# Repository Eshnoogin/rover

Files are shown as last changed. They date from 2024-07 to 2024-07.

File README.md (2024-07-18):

# Version 1



This version of the rover has to be plugged in to work, or be powered by a battery that supplies more than 5 volts. It integrates three motor drivers and a gyroscope to correct for the motors' speeds being slightly off from each other.  It has three almost 3d printed omniwheels, which only need ball bearings and screws. It uses an ESP-32 dev board to drive the motors. It also has ESP-NOW integration, which is needed in order to be driven by an external joystick.

# Version 2 - WIP
roverv2
This version of the rover supports being completely battery powered with two AA batteries. It is powered by an ESP32-S3, which uses a 3.3 volt regulator. The regulator is also powering the gyroscope and camera *eventually*. Onboard the PCB, there is also a 5v regulator to move the motors. Unlike V1 of the rover, these wheels are completely 3d printed. Unfortunatly, as of right now, the USB connection stopped working after a short and the motors are stuck spinning until shutdown.

# Board 

Version 2 of the board has four layers, with the two internal planes being ground planes, unlike version 1, which just has two layers and a ground fill on each. It uses a Texas Instraments DRV8832DGQR and TPS61040DBVRG4 to drive the motors and boost voltage, respectively. The gyroscope being used is part of the MPU-6050 and, of course, the main component of V2 is the ESP32-S3-WROOM module.

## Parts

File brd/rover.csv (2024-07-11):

Id | Designator | Footprint | Quantity | Designation | Supplier and ref
1 | R11,R12 | res1206 | 2 | 200kOhms
2 | R3,R1,R2 | res1206 | 3 | 2.87kOhms
3 | D1,D2 | D_SOD-123 | 2 | Schtokky
4 | C7 | cap1206 | 1 | 22uF
5 | R7,R19,R8,R9 | res1206 | 4 | 10kOhms
6 | P1 | PinHeader_1x02_P2.54mm_Vertical | 1 | ~
7 | P3,P4,P2 | twopad | 3 | ~
8 | C11,C13,C5,C10 | cap1206 | 4 | 4.7uF
9 | R6,R5,R4 | res1206 | 3 | 400mOhms
10 | C6 | cap1206 | 1 | 3.3pF
11 | C2,C1,C3 | cap1206 | 3 | 10uF
12 | J1 | MOLEX_1050170001 | 1 | 1050170001
13 | U2,U3,U1 | IC_XTR111AIDGQRG4 | 3 | DRV8832DGQR
14 | R10 | res1206 | 1 | 620kOhms
15 | U7 | XCVR_ESP32S3WROOM1N8R8 | 1 | ESP32-S3-WROOM-1-N4
16 | R13 | res1206 | 1 | 330kOhms
17 | U4,U5 | PinSocket_1x08_P2.54mm_Vertical | 2 | ~
18 | S2,S1 | SW_SKQGAFE010 | 2 | SKQGAFE010
19 | L1 | IND_SRR1240-100M | 1 | 3.3uH
20 | C4,C9 | cap1206 | 2 | .1uF
21 | C8 | cap1206 | 1 | 1uF
22 | U9,U6 | SOT95P280X145-5N | 2 | TPS61040DBVRG4
23 | L2 | IND_SRR1240-100M | 1 | 10uH

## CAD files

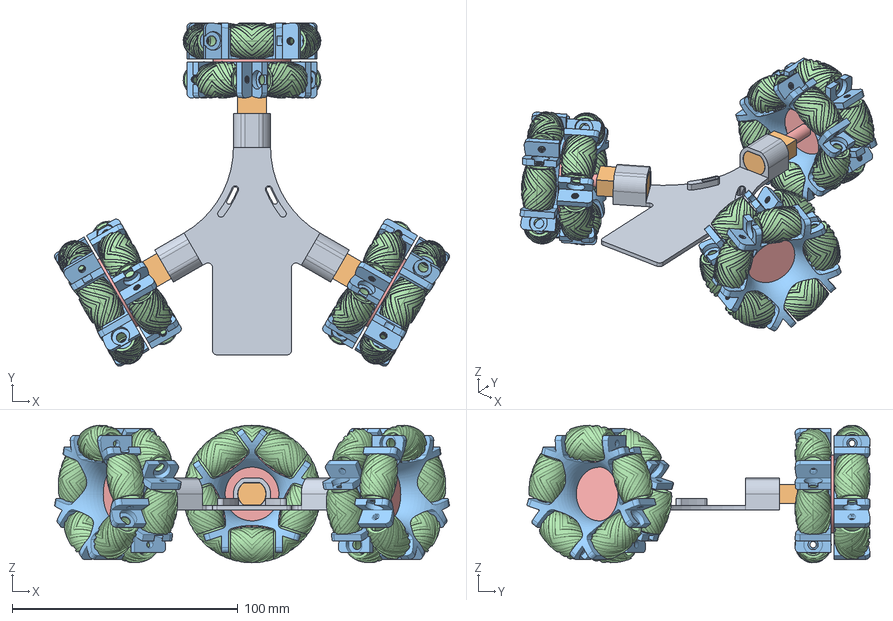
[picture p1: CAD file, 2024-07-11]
cad/rover.step
175.1 x 152.2 x 61.0 mm
motor x 3
base x 6
wheel x 30
middleJoint x 3

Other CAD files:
cad/rover.f3z

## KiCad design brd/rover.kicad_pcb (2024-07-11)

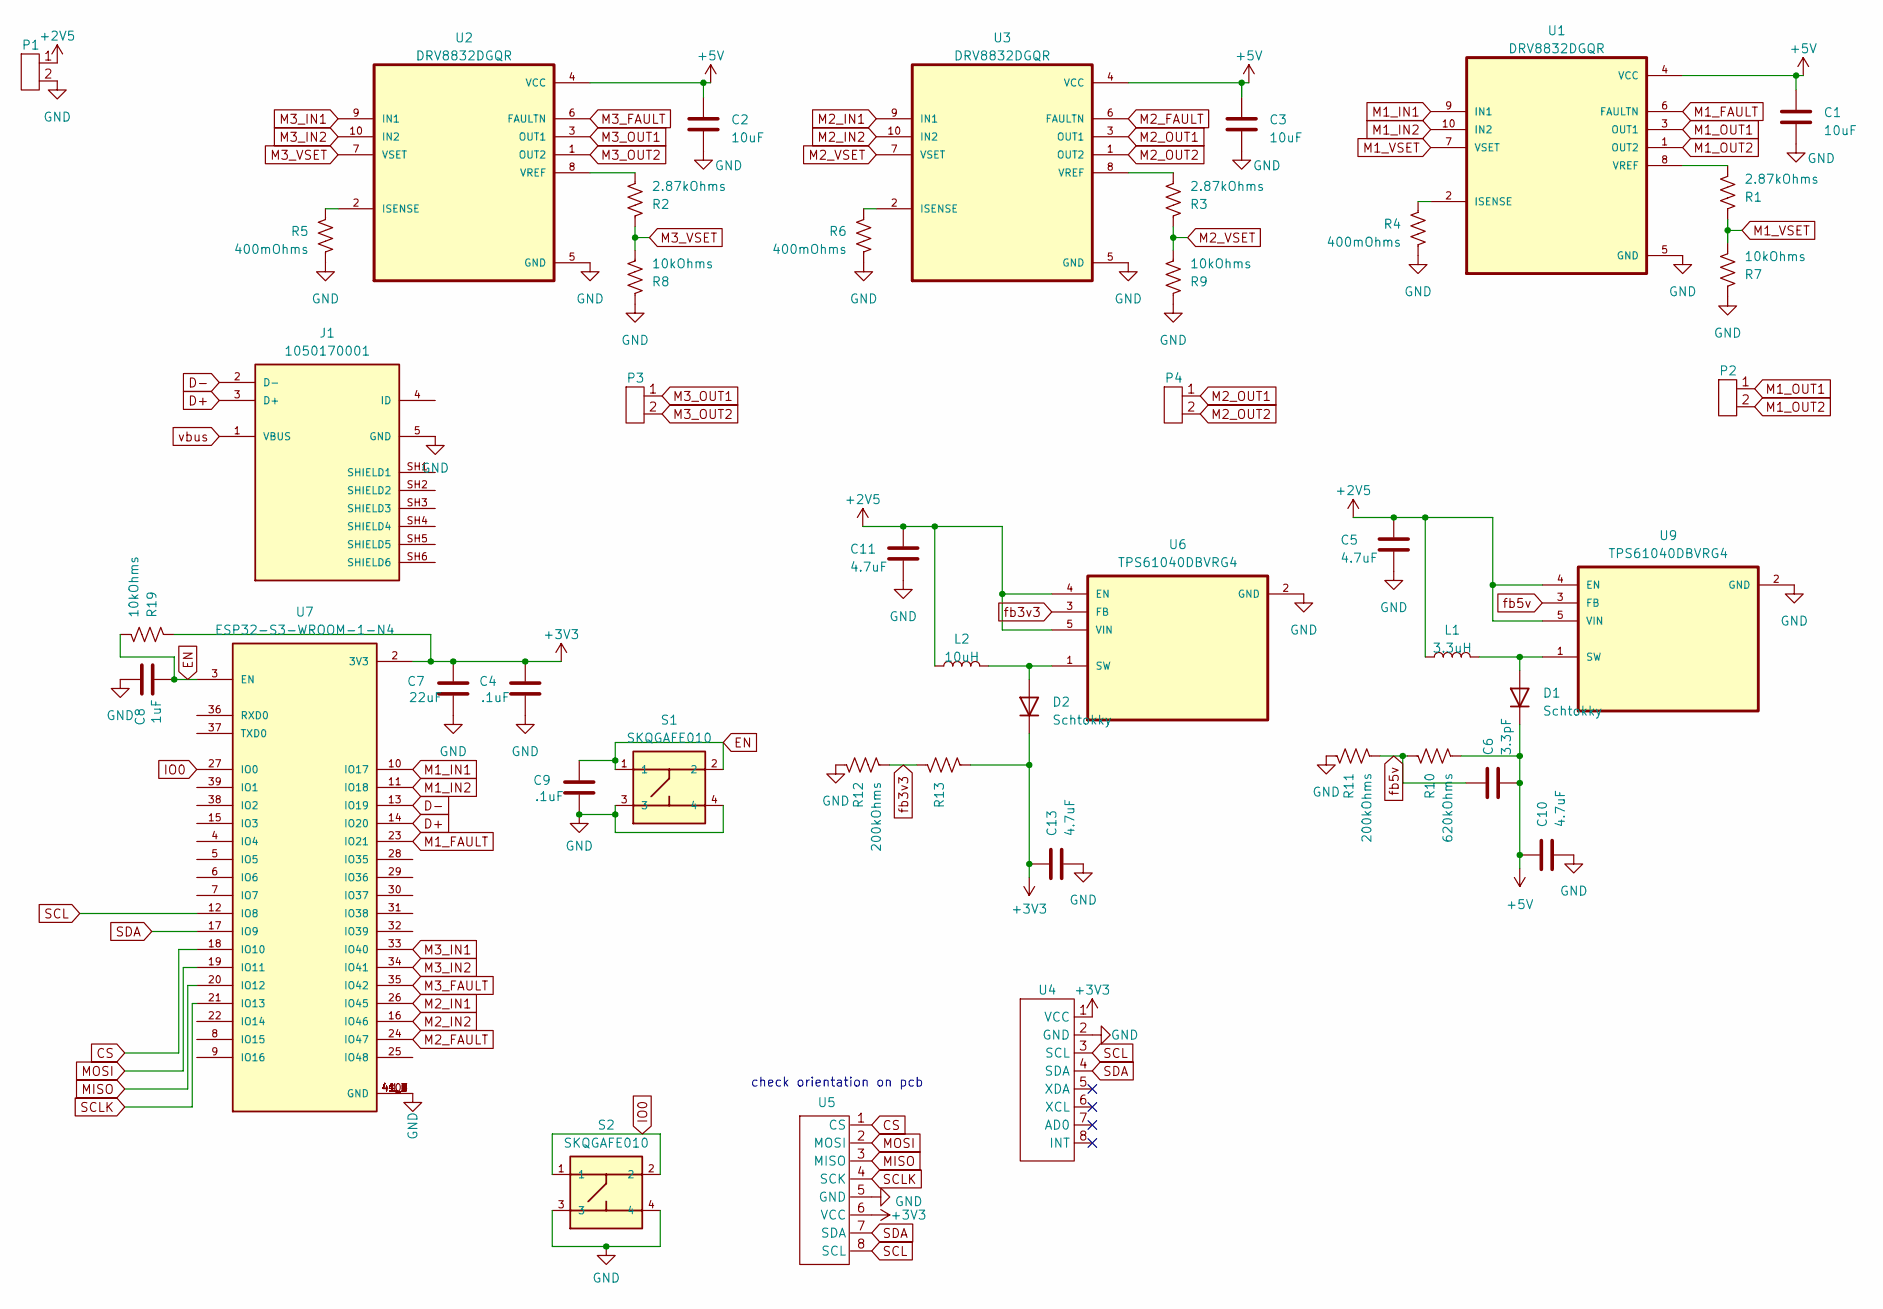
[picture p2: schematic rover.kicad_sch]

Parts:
C1, C2, C3: 10uF; cap1206
C4, C9: .1uF; cap1206
C5, C10, C11, C13: 4.7uF; cap1206
C6: 3.3pF; cap1206
C7: 22uF; cap1206
C8: 1uF; cap1206
D1, D2: Schtokky; D_SOD-123
J1: 1050170001; MOLEX_1050170001; PARTREV F
L1: 3.3uH; IND_SRR1240-100M
L2: 10uH; IND_SRR1240-100M
P1: PinHeader_1x02_P2.54mm_Vertical
P2, P3, P4: twopad
R1, R2, R3: 2.87kOhms; res1206
R4, R5, R6: 400mOhms; res1206
R7, R8, R9, R19: 10kOhms; res1206
R10: 620kOhms; res1206
R11, R12: 200kOhms; res1206
R13: 330kOhms; res1206
S1, S2: SKQGAFE010; SW_SKQGAFE010; PART_REV B1
U1, U2, U3: DRV8832DGQR; IC_XTR111AIDGQRG4
U4, U5: PinSocket_1x08_P2.54mm_Vertical
U6, U9: TPS61040DBVRG4; SOT95P280X145-5N
U7: ESP32-S3-WROOM-1-N4; XCVR_ESP32S3WROOM1N8R8; PARTREV v1.0

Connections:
+2V5: C5.1, C11.1, L1.1, L2.1, P1.1, U6.4 (EN), U6.5 (VIN), U9.4 (EN), U9.5 (VIN)
+3V3: C4.1, C7.1, C13.1, D2.1 (K), R13.2, R19.1, U4.1 (VCC), U5.6 (VCC), U7.2 (3V3)
+5V: C1.1, C2.1, C3.1, C6.2, C10.1, D1.1 (K), R10.2, U1.4 (VCC), U2.4 (VCC), U3.4 (VCC)
CS: U5.1 (CS), U7.18 (IO10)
D+: J1.3 (D+), U7.14 (IO20)
D-: J1.2 (D-), U7.13 (IO19)
EN: C8.2, C9.1, R19.2, S1.1, S1.2, U7.3 (EN)
GND: C1.2, C2.2, C3.2, C4.2, C5.2, C7.2, C8.1, C9.2, C10.2, C11.2, C13.2, J1.5 (GND), P1.2, R4.2, R5.2, R6.2, R7.1, R8.1, R9.1, R11.1, R12.1, S1.3, S1.4, S2.3, S2.4, U1.5 (GND), U2.5 (GND), U3.5 (GND), U4.2 (GND), U5.5 (GND), U6.2 (GND), U7.1 (GND), U7.40 (GND), U7.41_1 (GND), U7.41_2 (GND), U7.41_3 (GND), U7.41_4 (GND), U7.41_5 (GND), U7.41_6 (GND), U7.41_7 (GND), U7.41_8 (GND), U7.41_9 (GND), U9.2 (GND)
IO0: S2.1, S2.2, U7.27 (IO0)
M1_FAULT: U1.6 (FAULTN), U7.23 (IO21)
M1_IN1: U1.9 (IN1), U7.10 (IO17)
M1_IN2: U1.10 (IN2), U7.11 (IO18)
M1_OUT1: P2.1, U1.3 (OUT1)
M1_OUT2: P2.2, U1.1 (OUT2)
M1_VSET: R1.1, R7.2, U1.7 (VSET)
M2_FAULT: U3.6 (FAULTN), U7.24 (IO47)
M2_IN1: U3.9 (IN1), U7.26 (IO45)
M2_IN2: U3.10 (IN2), U7.16 (IO46)
M2_OUT1: P4.1, U3.3 (OUT1)
M2_OUT2: P4.2, U3.1 (OUT2)
M2_VSET: R3.1, R9.2, U3.7 (VSET)
M3_FAULT: U2.6 (FAULTN), U7.35 (IO42)
M3_IN1: U2.9 (IN1), U7.33 (IO40)
M3_IN2: U2.10 (IN2), U7.34 (IO41)
M3_OUT1: P3.1, U2.3 (OUT1)
M3_OUT2: P3.2, U2.1 (OUT2)
M3_VSET: R2.1, R8.2, U2.7 (VSET)
MISO: U5.3 (MISO), U7.20 (IO12)
MOSI: U5.2 (MOSI), U7.19 (IO11)
unnamed: D1.2 (A), L1.2, U9.1 (SW)
unnamed: D2.2 (A), L2.2, U6.1 (SW)
unnamed: R4.1, U1.2 (ISENSE)
unnamed: R1.2, U1.8 (VREF)
unnamed: R5.1, U2.2 (ISENSE)
unnamed: R2.2, U2.8 (VREF)
unnamed: R6.1, U3.2 (ISENSE)
unnamed: R3.2, U3.8 (VREF)
SCL: U4.3 (SCL), U5.8 (SCL), U7.12 (IO8)
SCLK: U5.4 (SCK), U7.21 (IO13)
SDA: U4.4 (SDA), U5.7 (SDA), U7.17 (IO9)
fb3v3: R12.2, R13.1, U6.3 (FB)
fb5v: C6.1, R10.1, R11.2, U9.3 (FB)
vbus: J1.1 (VBUS)

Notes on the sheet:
check orientation on pcb

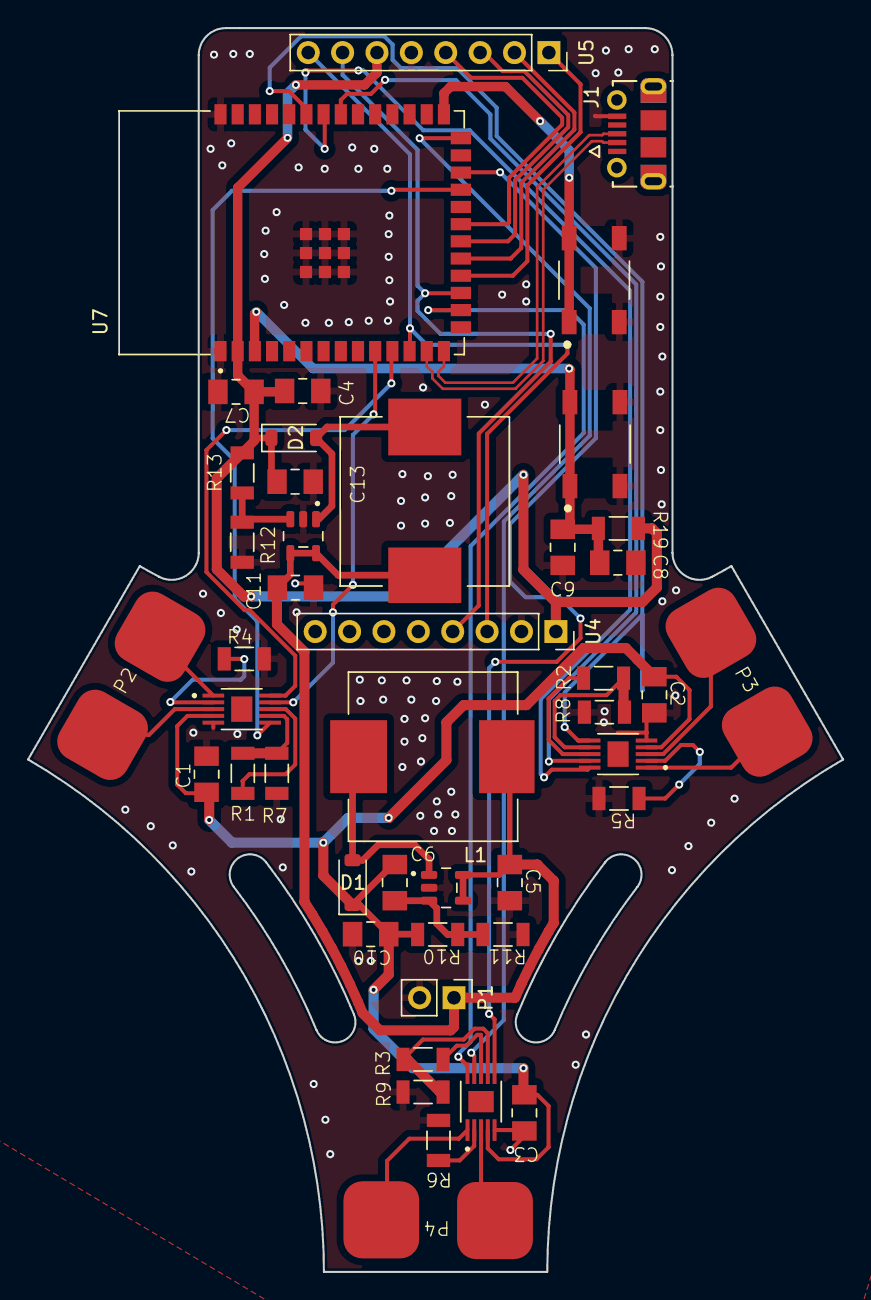
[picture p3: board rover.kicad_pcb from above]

Board: 4 copper layers, 60.2 x 91.9 mm, 45 parts (0 on the bottom side), 42 nets.

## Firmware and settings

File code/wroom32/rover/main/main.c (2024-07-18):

#include <stdio.h>
#include <math.h>

#include "freertos/FreeRTOS.h"
#include "esp_log.h"
#include "driver/i2c_master.h"
#include "driver/mcpwm_timer.h"
#include "driver/mcpwm_oper.h"
#include "driver/mcpwm_gen.h"
#include "driver/mcpwm_cmpr.h"
#include "esp_timer.h"
#include "driver/spi_master.h"

#include "driver/gpio.h"

#include "imu.h"
#include "common.h"
#include "motor.h"
#include "comm.h"
#include "cam.h"

#define TAG "RVR"

#define M1_IN1 26
#define M1_IN2 27
#define M2_IN1 16
#define M2_IN2 17
#define M3_IN1 32
#define M3_IN2 25

i2c_master_bus_handle_t i2c_mst_bus_handle;

imu_handle_t imu;

motor_handle_t motor1;
motor_handle_t motor2;
motor_handle_t motor3;

float measured_z_rotation;
SemaphoreHandle_t z_rot_mutex;

void handle_imu()
{
    while (1)
    {
        imu_update_gyro(&imu);

        CRITICAL_SECTION(imu.imu_mutex, 15, {
            CRITICAL_SECTION(z_rot_mutex, 15, {
                if (fabs(imu.gyro_z) > 10){ // some noise will be present in the raw sensor data
                    measured_z_rotation += imu.gyro_z;
                }
            });
        });

        vTaskDelay(10 / portTICK_PERIOD_MS);
    }
}

void handle_movement()
{
    while (1)
    {
        float v1 = 0;
        float v2 = 0;
        float v3 = 0;

        // read gyroscope data
        CRITICAL_SECTION(imu.imu_mutex, 15, {
            bool do_move = true;
            CRITICAL_SECTION(z_rot_mutex, 15, {
                if(fabs(measured_z_rotation) < 300){
                    do_move = false;
                }
                if(do_move){
                    if(fabs(measured_z_rotation) < 450){ //helps the robot face the center in less steps
                        v1 += (measured_z_rotation < 0) ? -0.25 : 0.25;
                        v2 += (measured_z_rotation < 0) ? -0.25 : 0.25;
                        v3 += (measured_z_rotation < 0) ? -0.25 : 0.25;     
                    }else{  
                        v1 += (measured_z_rotation < 0) ? -0.5 : 0.5;
                        v2 += (measured_z_rotation < 0) ? -0.5 : 0.5;
                        v3 += (measured_z_rotation < 0) ? -0.5 : 0.5;        
                    }
                }
            });
        });

        // read espnow data
        CRITICAL_SECTION(last_command.cmd_mutex, 15, {
            if(last_command.time + 20000 > esp_timer_get_time()){
                v1 += cos(last_command.direction);
                v2 += -.5 * cos(last_command.direction) + ((sqrt(3) / 2) * sin(last_command.direction));
                v3 += -.5 * cos(last_command.direction) - ((sqrt(3) / 2) * sin(last_command.direction));

                // normalize values
                float v_max = fmax(fabs(v1), fmax(fabs(v2), fabs(v3)));
                if (v_max != 0)
                {
                    v1 /= v_max;
                    v2 /= v_max;
                    v3 /= v_max;
                }
            }
        });

        ESP_LOGI(TAG, "M1: %f M2: %f M3: %f", v1, v2, v3);

        // move motors
        motor_move_at(&motor1, v1);
        motor_move_at(&motor2, v2);
        motor_move_at(&motor3, v3);

        vTaskDelay(pdMS_TO_TICKS(25));
    }
}

void app_main(void)
{
    // setup i2c for gyroscope and camera
    i2c_master_bus_config_t i2c_mst_config = {
        .clk_source = I2C_CLK_SRC_DEFAULT,
        .i2c_port = -1,
        .scl_io_num = 22,
        .sda_io_num = 21,
        .glitch_ignore_cnt = 7,
    };
    ESP_ERROR_CHECK(i2c_new_master_bus(&i2c_mst_config, &i2c_mst_bus_handle));

    // init imu
    z_rot_mutex = xSemaphoreCreateMutex();
    TaskHandle_t handle_imu_handler;
    imu_init(&imu);
    xTaskCreate(handle_imu, "handle_imu", 4096, NULL, 1, &handle_imu_handler);

    // configure timer, shared across all pwms
    ledc_fade_func_install(0);
    ledc_timer_config_t ledc_timer = {
        .speed_mode = LEDC_LOW_SPEED_MODE,
        .timer_num = LEDC_TIMER_0,
        .duty_resolution = LEDC_TIMER_8_BIT,
        .freq_hz = 25,
        .clk_cfg = LEDC_AUTO_CLK};
    ledc_timer_config(&ledc_timer);

    // init motors
    motor_init(&motor1, M1_IN1, M1_IN2, LEDC_CHANNEL_0, LEDC_CHANNEL_1, &ledc_timer);
    motor_init(&motor2, M2_IN1, M2_IN2, LEDC_CHANNEL_2, LEDC_CHANNEL_3, &ledc_timer);
    motor_init(&motor3, M3_IN1, M3_IN2, LEDC_CHANNEL_4, LEDC_CHANNEL_5, &ledc_timer);

    // setup esp-now
    espnow_init();

    // init movement
    TaskHandle_t handle_movement_handler;
    xTaskCreate(handle_movement, "handle_movement", 2048, NULL, 1, &handle_movement_handler);

    ESP_LOGI(TAG, "startSTART");
    for(int i=0; i<=255; i++){
        ESP_LOGI(TAG, "probing 0x%.2x", i);
        if(i2c_master_probe(i2c_mst_bus_handle, i, 100) == ESP_OK){
            ESP_LOGW(TAG, "DEV FOUND AT 0x%.2x", i);
        }
    }

    //init SPI bus
    spi_bus_config_t spi_bus_config = {
        .data0_io_num=-1,
        .data1_io_num=-1,
        .data2_io_num=-1,
        .data3_io_num=-1,
        .data4_io_num=-1,
        .data5_io_num=-1,
        .data6_io_num=-1,
        .data7_io_num=-1,
        .miso_io_num=19,
        .mosi_io_num=23,
        .quadhd_io_num=-1,
        .quadwp_io_num=-1,
        .sclk_io_num=18
    };

    spi_bus_initialize(SPI2_HOST, &spi_bus_config, SPI_DMA_CH_AUTO);

    //init arducam
    cam_handle_t cam_handle;
    cam_init(&cam_handle);

}

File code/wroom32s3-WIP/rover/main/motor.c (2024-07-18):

#include "driver/ledc.h"
#include "math.h"

#include "esp_log.h"

#include "motor.h"

const char *TAG = "MVMT";


esp_err_t motor_init(
    motor_handle_t *handle,
    int gpio_in_1, int gpio_in_2,
    ledc_channel_t channel_in_1,
    ledc_channel_t channel_in_2,
    ledc_timer_config_t *timer_config)
{
    // configure pwm for in1
    ledc_channel_config_t m1_ledc_channel = {
        .gpio_num = gpio_in_1,
        .speed_mode = LEDC_LOW_SPEED_MODE,
        .channel = channel_in_1,
        .intr_type = LEDC_INTR_DISABLE,
        .timer_sel = timer_config->timer_num,
        .duty = 0,
        .hpoint = 0, // start point of the pwm signal 
    };
    ESP_ERROR_CHECK(ledc_channel_config(&m1_ledc_channel));

    // configure pwm for in2
    ledc_channel_config_t m2_ledc_channel = {
        .gpio_num = gpio_in_2,
        .speed_mode = LEDC_LOW_SPEED_MODE,
        .channel = channel_in_2,
        .intr_type = LEDC_INTR_DISABLE,
        .timer_sel = timer_config->timer_num,
        .duty = 0,
        .hpoint = 0, // start point of the pwm signal 
    };
    ESP_ERROR_CHECK(ledc_channel_config(&m2_ledc_channel));

    handle->in_1 = channel_in_1;
    handle->in_2 = channel_in_2;
    handle->max_duty = pow(2, (int)timer_config->duty_resolution) - 1;

    ESP_LOGI(TAG, "Motor created at channels %i and %i", channel_in_1, channel_in_2);

    return ESP_OK;
}

esp_err_t motor_stop(motor_handle_t *handle)
{
    if (handle->is_moving)
    {
        ESP_LOGI(TAG, "Stopping motor at channels %i and %i", handle->in_1, handle->in_2);

        // set in1 and in2 to 0 to stop motor
        ESP_ERROR_CHECK(ledc_set_duty_and_update(LEDC_LOW_SPEED_MODE, handle->in_1, 0, 0));
        ESP_ERROR_CHECK(ledc_set_duty_and_update(LEDC_LOW_SPEED_MODE, handle->in_2, 0, 0));

        // update state
        handle->is_moving = false;

        return ESP_OK;
    }

    return ESP_OK;
}

esp_err_t motor_move_at(motor_handle_t *handle, float duty_percent)
{
    if (duty_percent == 0)
    {
        motor_stop(handle);
        return ESP_OK;
    }

    int calcuated_duty = fabs((duty_percent)*handle->max_duty);
    ESP_LOGI(TAG, "Moving motor at channels %i and %i with a duty cycle of %i", handle->in_1, handle->in_2, calcuated_duty);

    if (duty_percent <= 0)
    {
        // in1 goes to duty cycle and in2 goes low
        ESP_ERROR_CHECK(ledc_set_duty(LEDC_LOW_SPEED_MODE, handle->in_1, calcuated_duty));
        ESP_ERROR_CHECK(ledc_set_duty(LEDC_LOW_SPEED_MODE, handle->in_2, 0));
    }
    else
    {
        // in2 goes to duty cycle and in1 goes low
        ESP_ERROR_CHECK(ledc_set_duty(LEDC_LOW_SPEED_MODE, handle->in_2, calcuated_duty));
        ESP_ERROR_CHECK(ledc_set_duty(LEDC_LOW_SPEED_MODE, handle->in_1, 0));
    }

    ledc_update_duty(LEDC_LOW_SPEED_MODE, handle->in_1);
    ledc_update_duty(LEDC_LOW_SPEED_MODE, handle->in_2);

    // update state
    handle->is_moving = true;

    return ESP_OK;
}
